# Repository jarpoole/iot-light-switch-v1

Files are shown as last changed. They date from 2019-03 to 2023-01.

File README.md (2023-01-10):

# iot-light-switch-v1

See V2 ([iot-light-switch-v2](https://github.com/jarpoole/iot-light-switch-v2)) for a second more polished attempt at this concept.

## Features

1. Voice control through google-assisant.
2. Tool-less magnetic installation.
3. DC barrel jack backup power source.

## Limitations

1. Not compatible with rocker style switches.
2. Not compatible with double switches.
3. Short battery life without the option to recharge.
4. Complex hardware with both an `ESP8266` to connect to the internet and an `Arduino NANO` to control the servo.

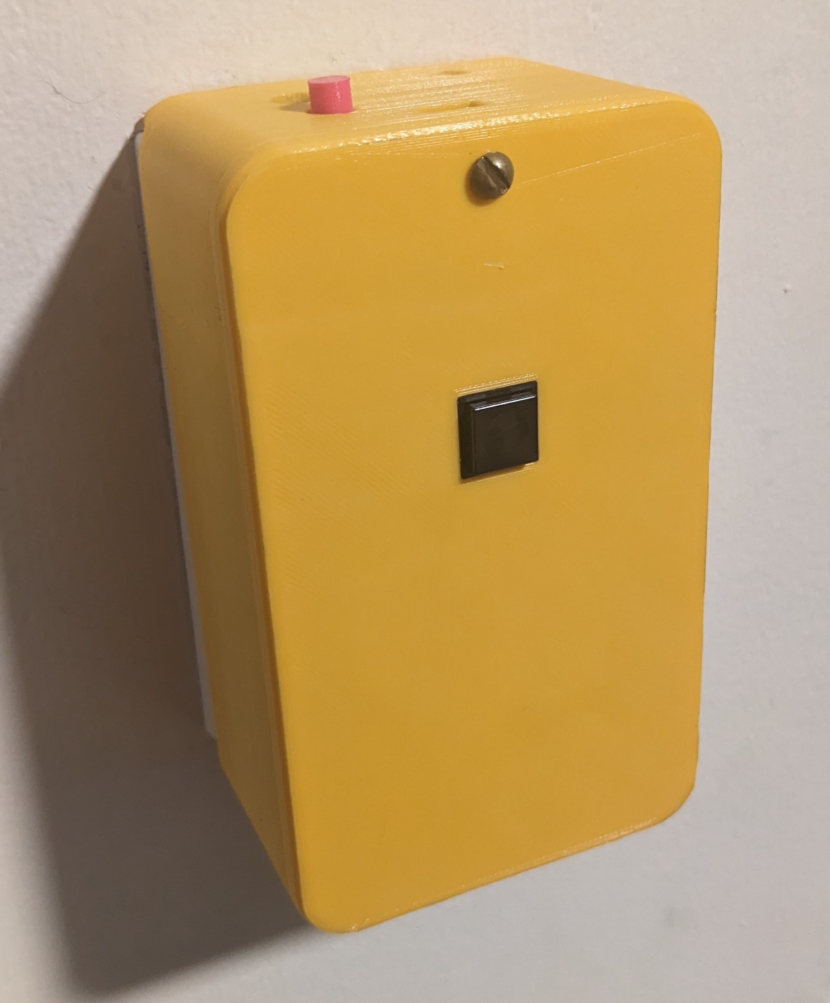
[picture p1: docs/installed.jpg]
installed


## Internals

assembly

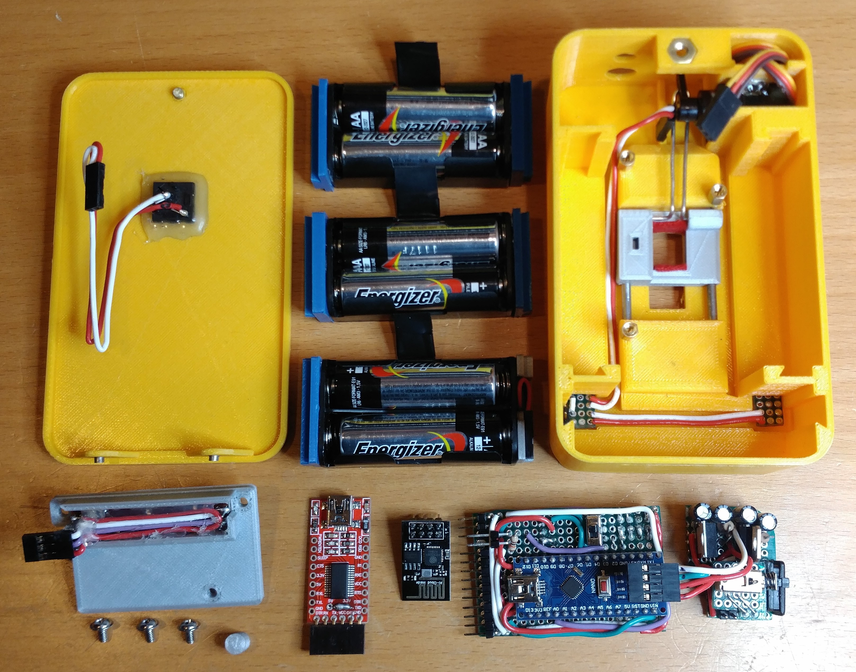
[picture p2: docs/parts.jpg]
parts


## Mechanical

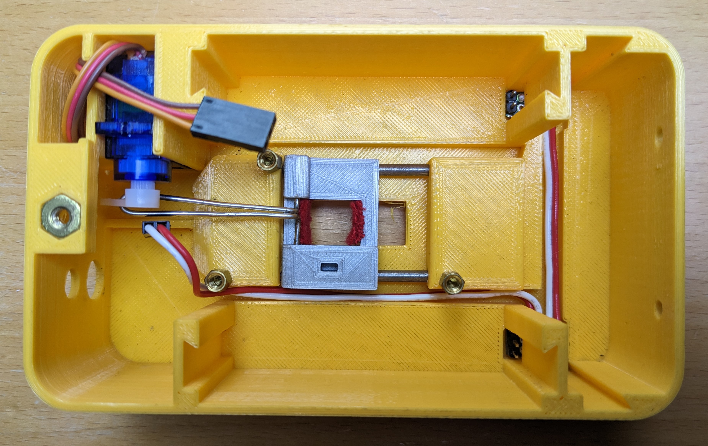
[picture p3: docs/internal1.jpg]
internal1


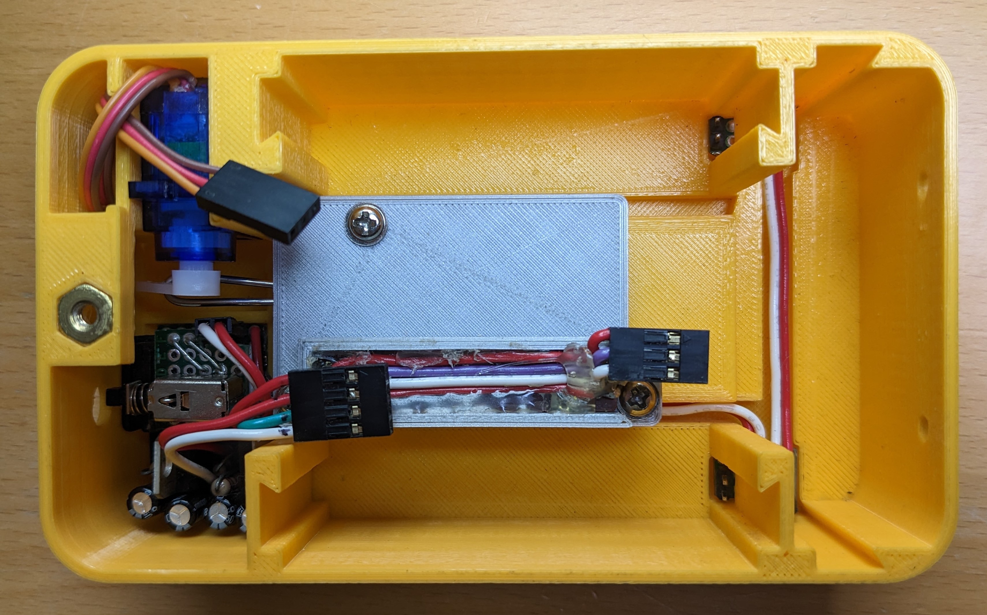
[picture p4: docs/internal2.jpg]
internal2


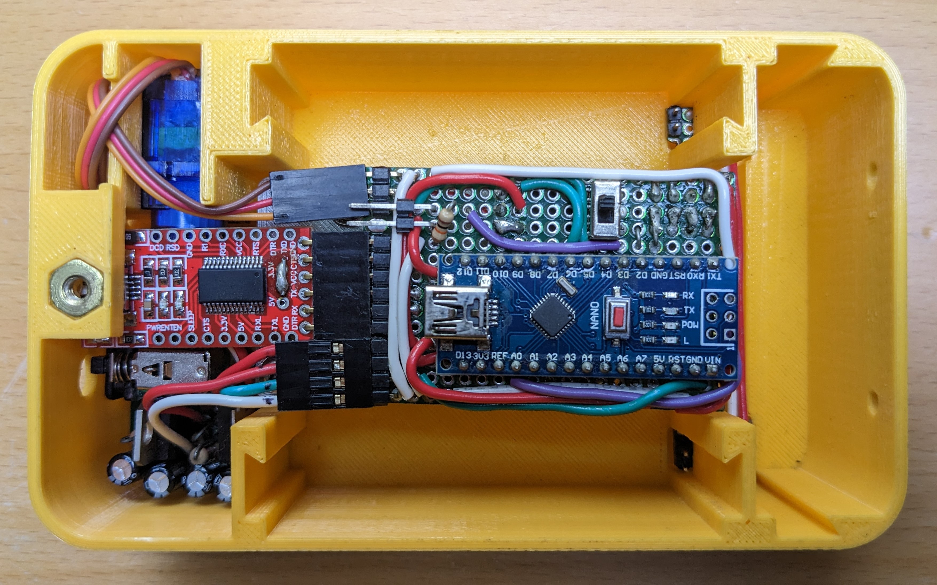
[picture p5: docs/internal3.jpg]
internal3


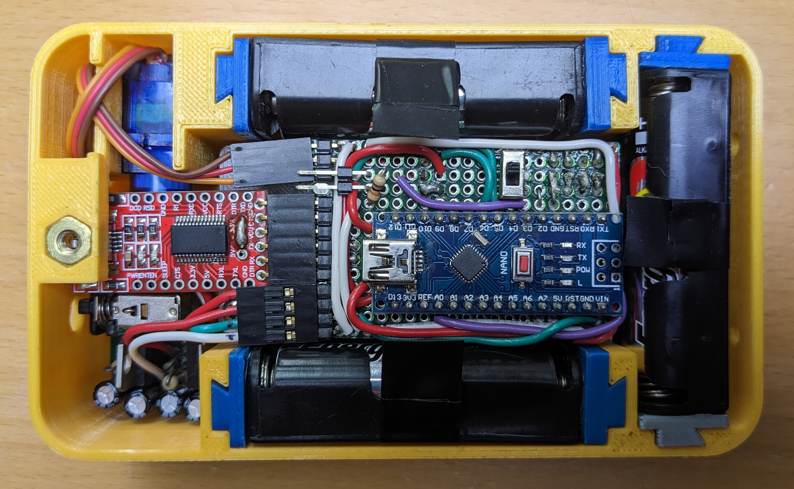
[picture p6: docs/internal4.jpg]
internal4


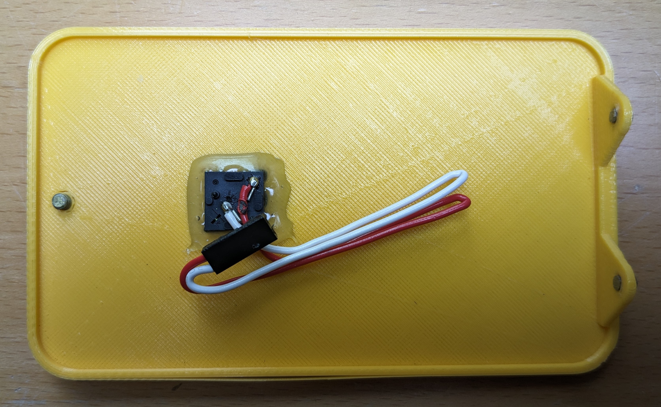
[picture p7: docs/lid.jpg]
lid


## Electrical

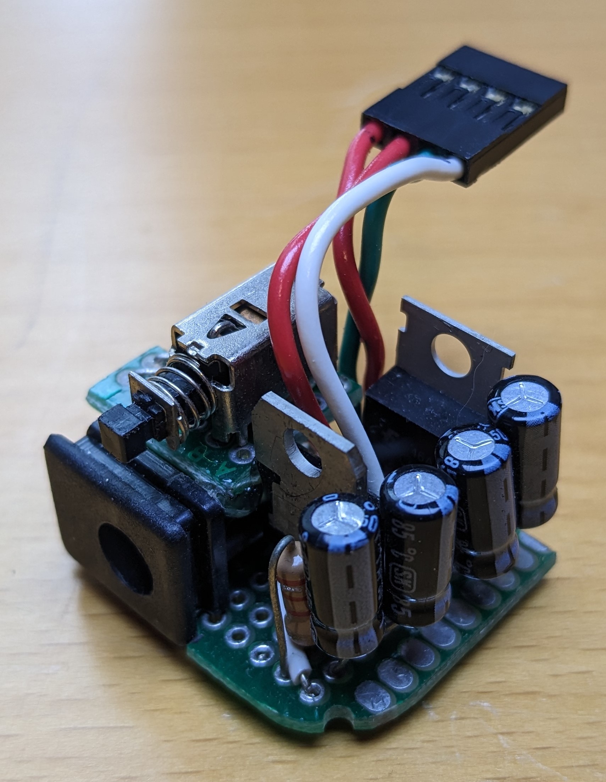
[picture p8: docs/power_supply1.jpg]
powersupply


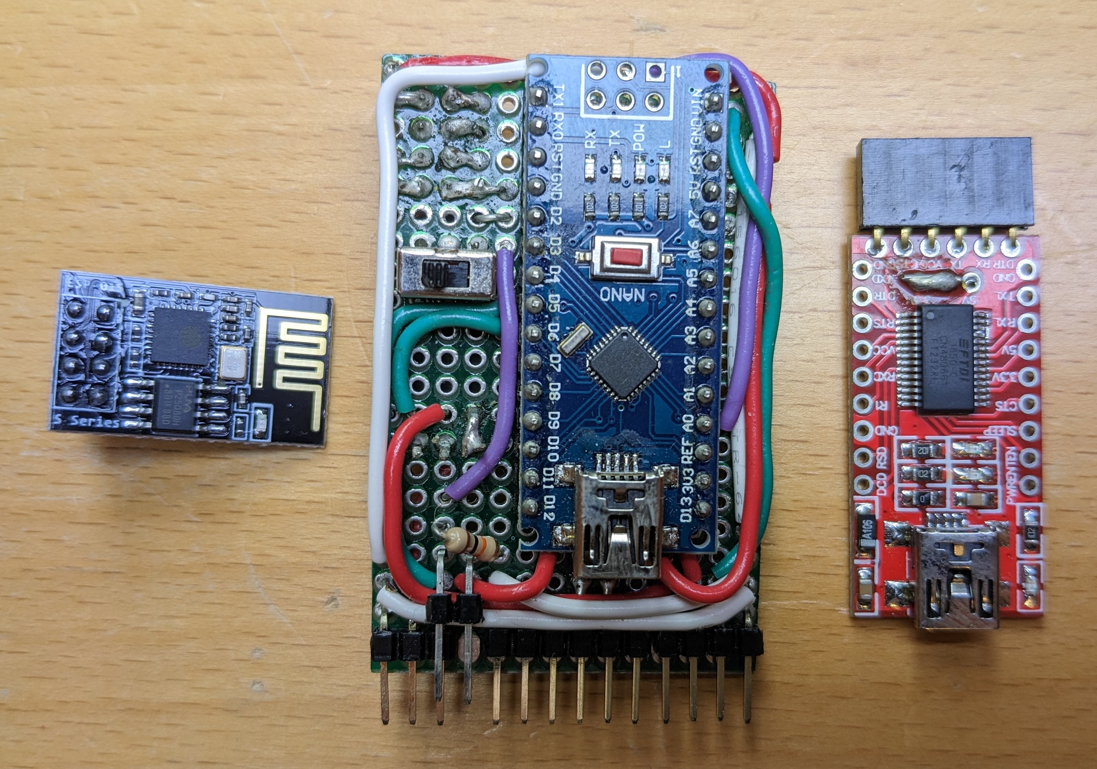
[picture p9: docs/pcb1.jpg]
mainboard


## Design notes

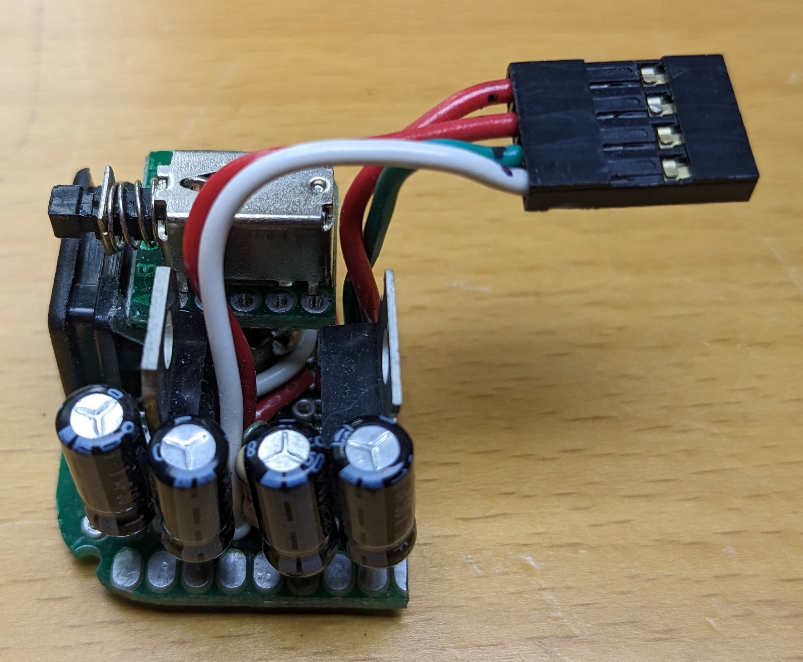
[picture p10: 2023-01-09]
docs/power_supply2.jpg

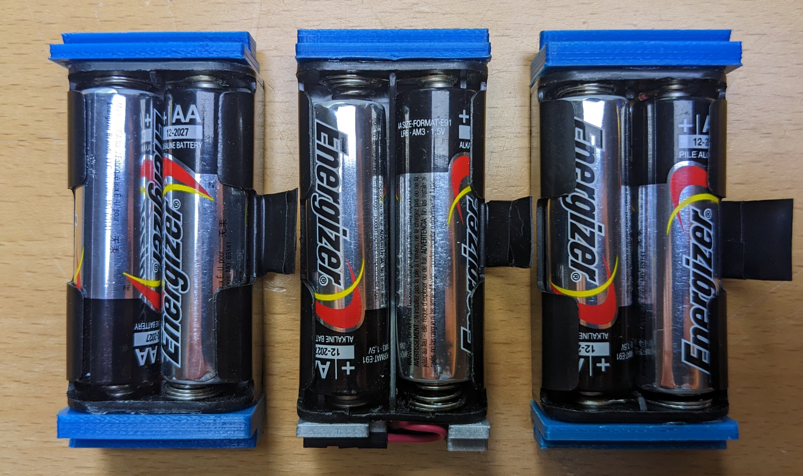
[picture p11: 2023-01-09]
docs/battery.jpg

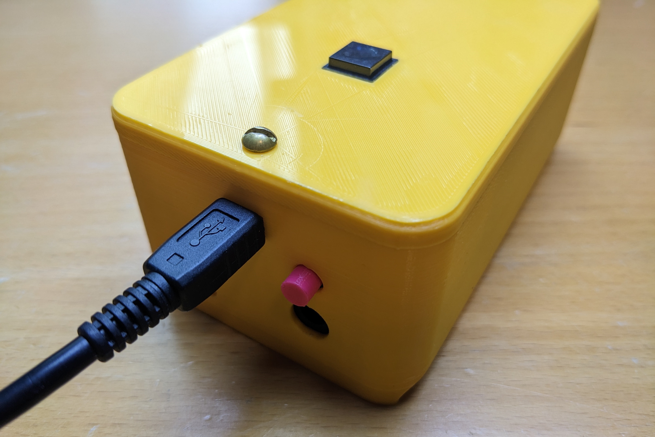
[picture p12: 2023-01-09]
docs/io.jpg

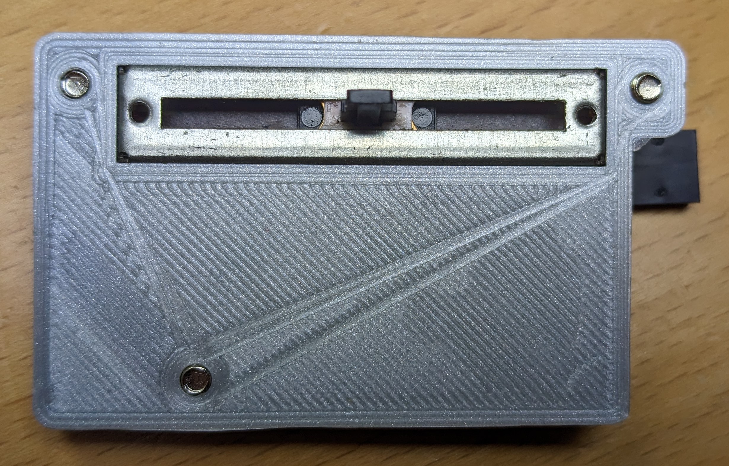
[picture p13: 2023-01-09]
docs/potentiometer.jpg

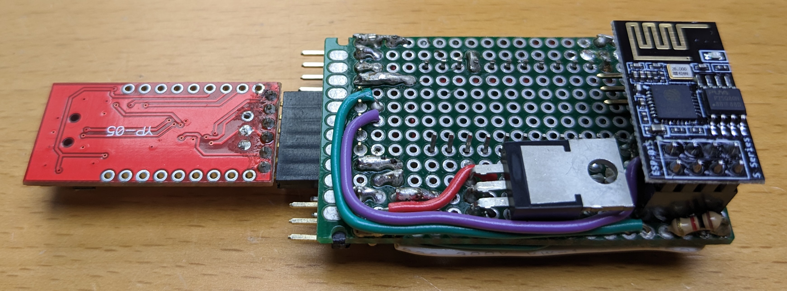
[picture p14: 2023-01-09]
docs/pcb2.jpg

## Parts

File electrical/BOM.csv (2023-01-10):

Part Number | Part Name | Supplier | Description | Unit Cost | Quantity | Extended Cost
36-2463-ND | MG90D | Digikey | High torque metal geared servo | 14.44 | 1 | 14.44
1189-1300-ND | Capacitor | Digikey | Radial 100uF Capacitor | 0.43 | 4 | 1.72
497-1485-5-ND | LD1117A | Digikey | 3.3v linear voltage regulator | 0.82 | 1 | 0.82
497-15681-5-ND | L7805 | Digikey | 5v linear voltage regulator | 0.96 | 1 | 0.96
FDP6030BL-ND | MOSFET | Digikey | 30v 40A mosfet | 2.23 | 1 | 2.23
CKN4080-ND | Activation witch | Digikey | SPST push button switch | 2.17 | 1 | 2.17
CKN9565-ND | Programming Switch | Digikey | DPST sliding switch | 0.62 | 1 | 0.62
CKN1188-ND | Power Switch | Digikey | SPDT latching push button | 1.89 | 1 | 1.89
S7072-ND | Female Header | Digikey | 8 pos 0.1 inch pitch female header | 0.95 | 1 | 0.95
S2112EC-40-ND | Male Header | Digikey | 8 pos 0.1 inch x2 pitch male header | 2.52 | 1 | 2.52
36-2463-ND | Battery Holder | Digikey | 2x AA battery holder pack | 1.72 | 3 | 5.16
EJ508A-ND | Power Port | Digikey | 12v male power jack | 1.82 | 1 | 1.82
952-2229-ND | Female Header | Digikey | 4 pos crimping header | 0.27 | 1 | 0.27
952-2228-ND | Female Header | Digikey | 3 pos crimping header | 0.17 | 1 | 0.17
952-2227-ND | Female Header | Digikey | 2 pos crimping header | 0.23 | 3 | 0.69
952-2158-ND | Female Pin | Digikey | Standard 22-30AWG crimp pin | 0.12 | 13 | 1.56
36-8717-ND | Standoff | Digikey | #6-32 standoff | 0.71 | 3 | 2.13
36-8190-1-ND | Screw | Digikey | #6-32 mounting screws | 0.23 | 3 | 0.69
CF14JT10K0CT-ND | 10k Resistor | Digikey | 10k 1/4W through hole resistor | 0.15 | 1 | 0.15
PPC1.10KXCT-ND | 1.1k Resistor | Digikey | 1.1k 1/4W through hole resistor | 0.31 | 1 | 0.31
PTA3043-2010CIB103-ND | Slide Potentiometer | Digikey | Variable linear potentiometer | 2.13 | 1 | 2.13
S1111EC-40-ND | Male Header | Digikey | 40 pos 0.1 inch pitch right angle male header | 1.32 | 1 | 1.32
ESP8266 | Wi-Fi Module | Amazon | Low lowered Arduino Wi-Fi adapter | 14 | 1 | 14
ATmega328P | Arduino Nano | eBay | Arduino compatible microcontroller | 5.17 | 1 | 5.17
FT232RL | USB to Serial | eBay | USB to Serial FTDI adapter | 3.19 | 1 | 3.19

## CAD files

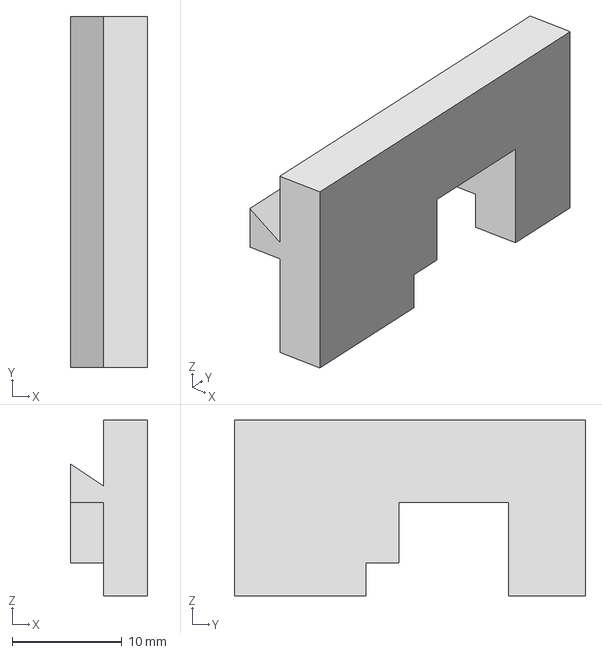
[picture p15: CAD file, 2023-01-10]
mechanical/battery_rail_3.stp
7.00 x 32.0 x 16.0 mm

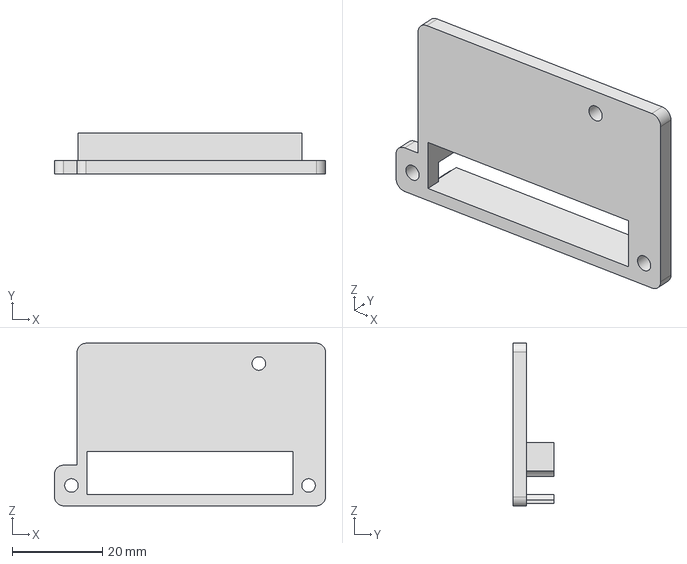
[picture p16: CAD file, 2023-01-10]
mechanical/midplate.stp
60.0 x 9.00 x 36.0 mm

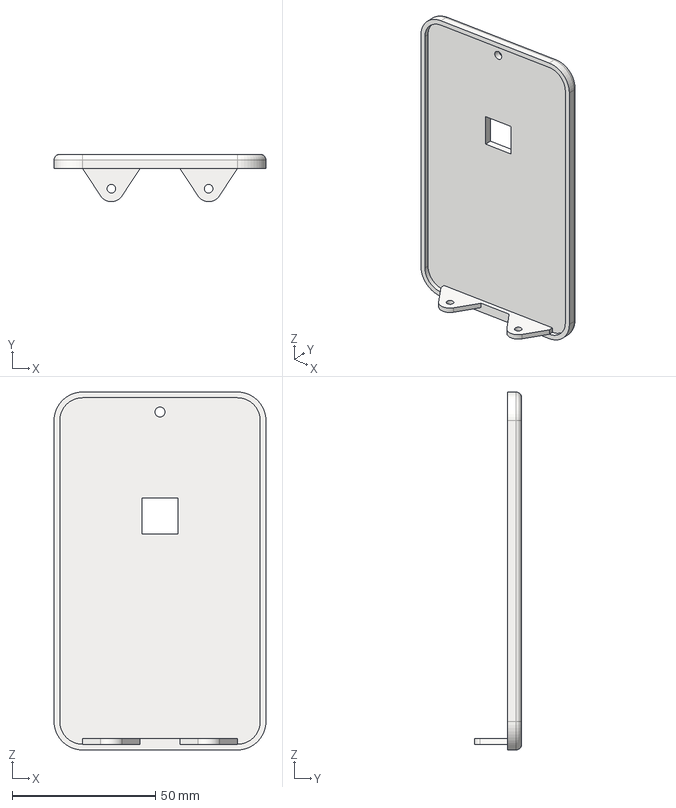
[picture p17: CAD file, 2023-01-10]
mechanical/cover.stp
74.0 x 16.5 x 125.0 mm

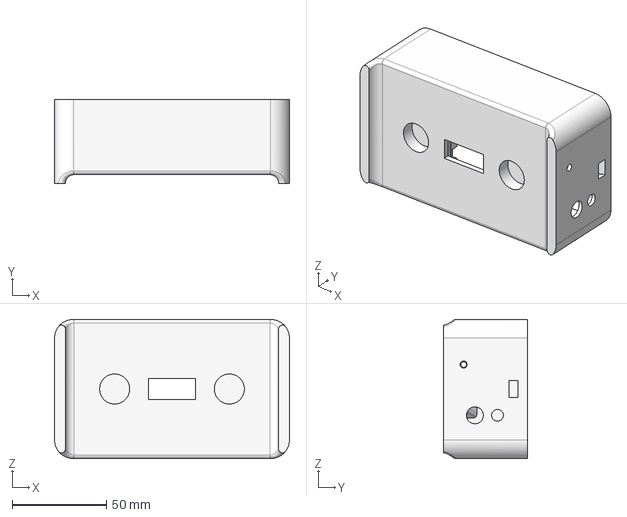
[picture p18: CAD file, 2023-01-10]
mechanical/case.stp
125.0 x 44.8 x 74.0 mm

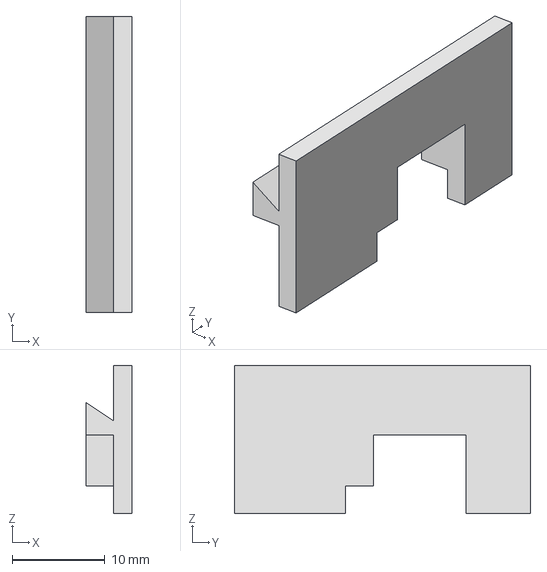
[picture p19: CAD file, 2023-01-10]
mechanical/battery_rail_4.stp
5.00 x 32.0 x 16.0 mm

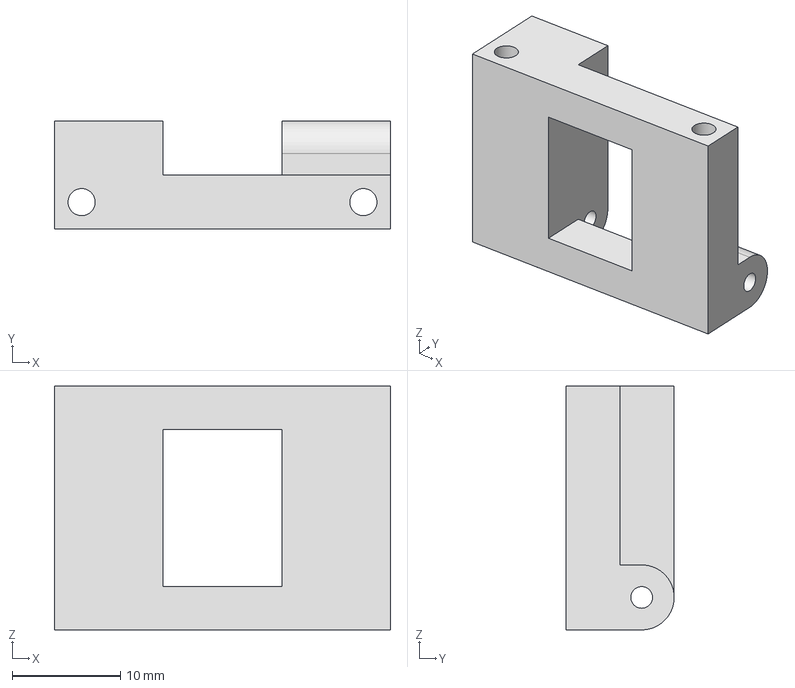
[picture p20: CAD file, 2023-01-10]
mechanical/carriage.stp
31.0 x 10.0 x 22.5 mm

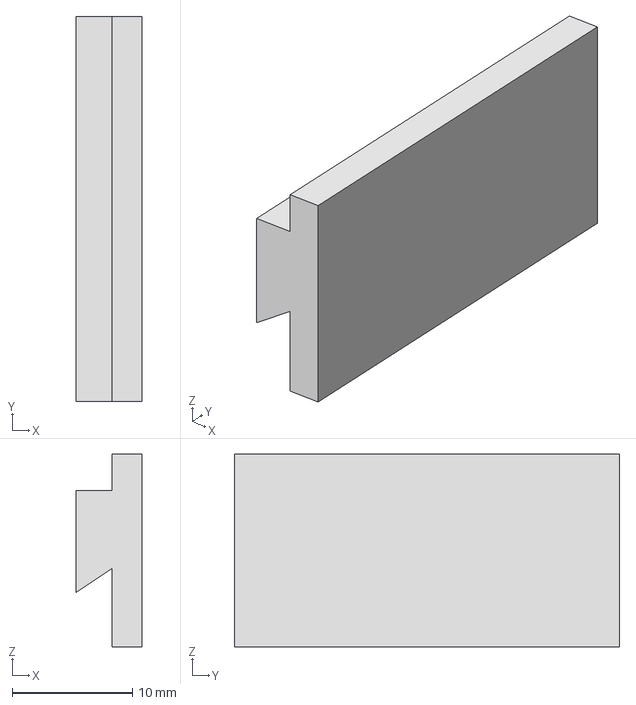
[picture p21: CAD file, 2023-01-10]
mechanical/battery_rail_1.stp
5.50 x 32.0 x 16.0 mm

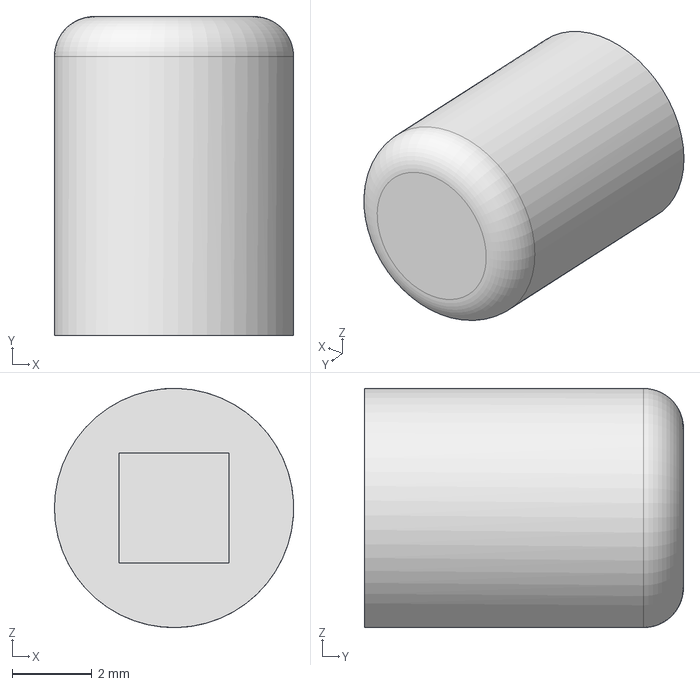
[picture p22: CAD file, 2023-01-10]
mechanical/button.stp
6.00 x 8.00 x 6.00 mm

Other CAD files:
mechanical/battery_rail_2.stp
mechanical/assembly.iam
mechanical/battery_rail_1.ipt
mechanical/battery_rail_2.ipt
mechanical/battery_rail_3.ipt
mechanical/battery_rail_4.ipt
mechanical/button.ipt
mechanical/carriage.ipt
mechanical/case.ipt
mechanical/cover.ipt
mechanical/midplate.ipt
mechanical/plate/assembly.iam
mechanical/plate/plate.ipt

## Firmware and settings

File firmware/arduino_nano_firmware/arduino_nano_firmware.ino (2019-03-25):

//#define DEBUG 1

#include "Servo.h"

//Interrupt Stuff
int interruptPin = 2;
unsigned long volatile lastInterruptTime = 0;
int minInterruptDelay = 1500;

//Serial Stuff
int hardwareBaudRate = 9600;
int softwareBaudRate = 9600;

//Motor Stuff
Servo motor;
int motorPWMPin = 5;
int motorEnablePin = 6;
int onMicroseconds = 1800; //up towards battery
int offMicroseconds = 800; //down towards power plug

unsigned long volatile lastMoveTime = 0;
int minMoveDelay = 500;

//Slider Stuff
int minimumOffPos = 500;      //actual = 566; aggressive = 500; conservative = 490;
int maximumOnPos = 180;     //actual = 154; aggressive = 190; conservative = 200;
int slideResistorPin = A0;
int slideResistorPos = 0;

//Switch state Stuff
bool switchOn = true;
bool unprocessedMove = false;
bool moving = false;

//Button stuff
int buttonPin = 3;

void setup() {
  #ifdef DEBUG
    Serial.begin(hardwareBaudRate);
  #endif
  
  pinMode(13,OUTPUT);
  
  motor.attach(motorPWMPin);
  pinMode(motorEnablePin, OUTPUT);

  pinMode(interruptPin, INPUT);
  attachInterrupt(0, processInterrupt, RISING);

  pinMode(buttonPin, INPUT);
  attachInterrupt(1, processInterrupt, RISING);

  turnOn();

  //digitalWrite(motorEnablePin, HIGH); //This is used as a global servo enable; Keep disabled by default
}

void processInterrupt(){
  if(!moving){
    unsigned long currentMillis = millis();
    if ((unsigned long)(currentMillis - lastInterruptTime) >= minInterruptDelay) {
      unprocessedMove = true;
      lastInterruptTime = currentMillis;
    }
  }
}

void loop() {
  #ifdef DEBUG
    Serial.println("Idle");
  #endif
  
  delay(100);
  update();
  
}

void update(){

  if(moving){
    unsigned long currentMillis = millis();
    if ((unsigned long)(currentMillis - lastMoveTime) >= minMoveDelay) {
      digitalWrite(motorEnablePin, LOW);
      moving = false;
      #ifdef DEBUG
        Serial.println("End Movement");
      #endif
    }
    return;

  }else if(unprocessedMove){
    switchOn = checkPos(true);
    #ifdef DEBUG
      Serial.println("Start Movement");
    #endif
    
    if(switchOn){
      turnOff();
    }else{
      turnOn();
    }
    unprocessedMove = false;
  }
}

void turnOn(){
  motor.writeMicroseconds(onMicroseconds);
  digitalWrite(motorEnablePin, HIGH);
  moving = true;
 
  digitalWrite(13,HIGH); //Debug

  lastMoveTime = millis();
  
  #ifdef DEBUG
      Serial.println("Turn on");
  #endif
  
  //digitalWrite(motorEnablePin, LOW);
  
  //if(!checkPos(true)){
    //turnOff();
  //}
  
}

void turnOff(){
  
  motor.writeMicroseconds(offMicroseconds);
  digitalWrite(motorEnablePin, HIGH);
  moving = true;
  
  digitalWrite(13,LOW);  //Debug
  
  lastMoveTime = millis();

  #ifdef DEBUG
    Serial.println("Turn off");
  #endif

  //digitalWrite(motorEnablePin, LOW);

  //if(!checkPos(false)){
    //turnOn();
  //}
  
}

//True for up/on, false for down/off
bool checkPos(bool on){
  slideResistorPos = analogRead(slideResistorPin);

  #ifdef DEBUG
    Serial.print("Slide Pos: ");
    Serial.println(slideResistorPos);
  #endif

  if(on){
    return slideResistorPos < maximumOnPos;
  }else{
    return slideResistorPos > minimumOffPos;
  }
}

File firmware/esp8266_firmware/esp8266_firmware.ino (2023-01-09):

//#define DEBUG 1

#include <ESP8266WiFi.h>
#include "Adafruit_MQTT.h"
#include "Adafruit_MQTT_Client.h"

// WiFi Sign-in information
#define WLAN_SSID       ""
#define WLAN_PASS       ""

// Adafruit IO Sign-in information
#define AIO_SERVER      "io.adafruit.com"
#define AIO_SERVERPORT  1883
#define AIO_USERNAME    ""
#define AIO_KEY         ""
#define AIO_FEED        "/feeds/LightSwitch"

WiFiClient client;

const char MQTT_SERVER[] PROGMEM    = AIO_SERVER;
const char MQTT_CLIENTID[] PROGMEM  = AIO_KEY __DATE__ __TIME__;
const char MQTT_USERNAME[] PROGMEM  = AIO_USERNAME;
const char MQTT_PASSWORD[] PROGMEM  = AIO_KEY;
Adafruit_MQTT_Client mqtt(&client, MQTT_SERVER, AIO_SERVERPORT, MQTT_CLIENTID, MQTT_USERNAME, MQTT_PASSWORD);

const char ONOFF_FEED[] PROGMEM = AIO_USERNAME AIO_FEED;

//Adafruit_MQTT_Subscribe OnOff = Adafruit_MQTT_Subscribe(&mqtt, ONOFF_FEED);
Adafruit_MQTT_Subscribe OnOff = Adafruit_MQTT_Subscribe(&mqtt, ONOFF_FEED, MQTT_QOS_1); //Attempts to connect with QOS level 1

//Interrupt Stuff
int interruptPin = 2;

void setup() {
  #ifdef DEBUG
    Serial.begin(9600);
 #endif
  
  pinMode(interruptPin, OUTPUT);
  
  #ifdef DEBUG
    Serial.println(F("Wifi Module Started"));
    Serial.println(); Serial.println();
    Serial.print(F("Connecting to "));
    Serial.println(WLAN_SSID);
  #endif

  // Connect to WiFi access point.
  delay(10);

  WiFi.persistent(false);
  WiFi.mode(WIFI_STA);
  
  WiFi.begin(WLAN_SSID, WLAN_PASS);
      
  #ifdef DEBUG
    while (WiFi.status() != WL_CONNECTED) {
      delay(500);
      Serial.print(F("."));
    }
    Serial.println();
    Serial.println(F("WiFi connected"));
    Serial.println(F("IP address: "));
    Serial.println(WiFi.localIP());
  #endif
  
  #ifndef DEBUG
    while (WiFi.status() != WL_CONNECTED) {
      WiFi.begin(WLAN_SSID, WLAN_PASS);
      delay(1000);
    }
  #endif

  mqtt.subscribe(&OnOff);
  connect();
  delay(500);
}

void loop() {
  #ifdef DEBUG
    Serial.println(F("Waiting"));
  #endif
  
  Adafruit_MQTT_Subscribe *subscription;

  
  // ping adafruit io a few times to make sure we remain connected
  if(! mqtt.ping(3)) {
    // reconnect to adafruit io
    if(! mqtt.connected())
      connect();
  }
    
  // this is our 'wait for incoming subscription packets' busy subloop
  while (subscription = mqtt.readSubscription(1000)) {

    // we only care about the OnOff events
    if (subscription == &OnOff) {
      
      #ifdef DEBUG
        Serial.println(F("Received"));
        delay(500);
      #endif
      
      digitalWrite(interruptPin, HIGH);
      delay(20);
      digitalWrite(interruptPin, LOW);
      /*
      // convert mqtt ascii payload to int
      char *value = (char *)OnOff.lastread;
      Serial.print(F("Received: "));
      Serial.println(value);

      // Apply message to OnOff
      String message = String(value);
      message.trim();
      if (message == "ON") {
        //digitalWrite(interruptPin, HIGH);
        Serial.println(F("ON"));
        }
      if (message == "OFF") {
        //digitalWrite(interruptPin, LOW);
        Serial.println(F("OFF"));
      }
      */

    }

  }

}


void connect() {
  #ifdef DEBUG
  Serial.print(F("Connecting to Adafruit IO... "));
  #endif
  
  int8_t ret;
  
  while ((ret = mqtt.connect()) != 0) {
    #ifdef DEBUG
    switch (ret) {
      case 1: Serial.println(F("Wrong protocol")); break;
      case 2: Serial.println(F("ID rejected")); break;
      case 3: Serial.println(F("Server unavail")); break;
      case 4: Serial.println(F("Bad user/pass")); break;
      case 5: Serial.println(F("Not authed")); break;
      case 6: Serial.println(F("Failed to subscribe")); break;
      default: Serial.println(F("Connection failed")); break;
    }
    #endif

    if(ret >= 0)
      mqtt.disconnect();

    #ifdef DEBUG
      Serial.println(F("Retrying connection..."));
    #endif
    delay(5000);

  }
  #ifdef DEBUG
  Serial.println(F("Adafruit IO Connected!"));
  #endif
}

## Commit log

2019-03-15 new file: Adafruit_IO_Test/Adafruit_IO_Test.ino new file: Arduino_ESP8266_Code/Arduino_ESP8266_Code.ino new file: Arduino_NANO_Code/Arduino_NANO_Code.ino
2023-01-09 More docs (#2)
    [assembly.iam, battery_rail_1.ipt, battery_rail_2.ipt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]
2023-01-10 Final Mechanical Docs (#3)
    [battery_rail_1.stp, battery_rail_2.stp, battery_rail_3.stp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]
2023-01-10 Added electrical (#4)
    [BOM.csv]
